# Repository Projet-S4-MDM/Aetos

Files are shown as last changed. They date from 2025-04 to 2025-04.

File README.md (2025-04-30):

# Aetos

Aetos is a vision-abled cable robot designed by 6 robotics engineering students from [Sherbrooke University](https://www.usherbrooke.ca/).

## Original Contributors

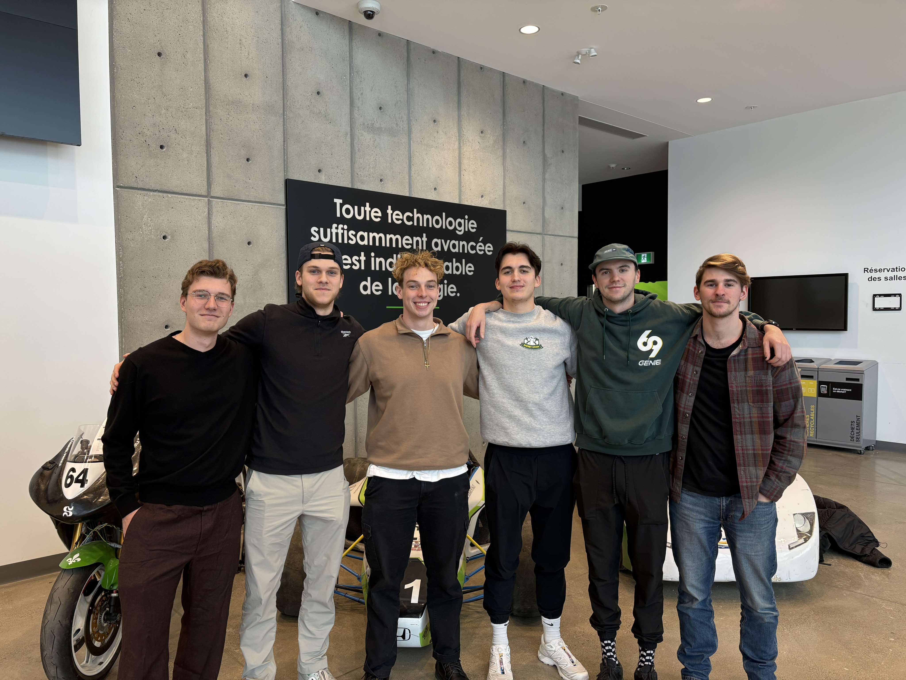
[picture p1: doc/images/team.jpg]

**From left to right:** Mathys Bousquet, Nathan Dumoulin, Édouard Lebel-Bernier, Nikolay Papanchez, Émile Savoie and David Ferron

## Final Product
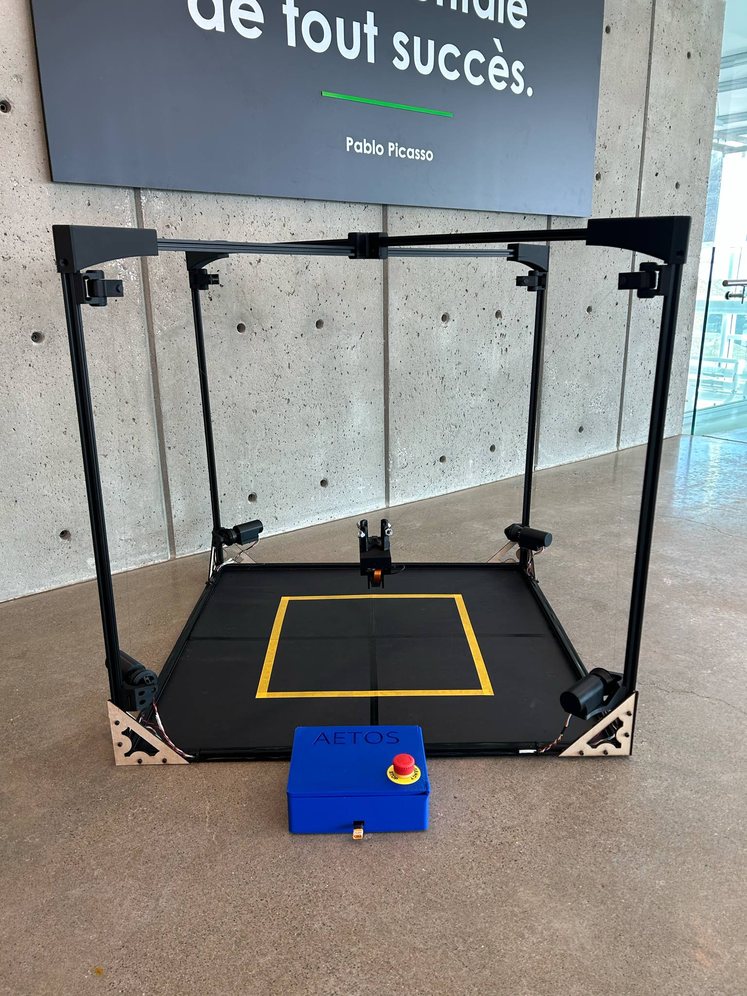
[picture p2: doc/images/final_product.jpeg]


## Documentation

The following links contain the documentation to build and operate the different elements of Aetos from scratch:

- [Mechanical Assembly](doc/Mechanical/mecanical_assembly.md)
- [Electrical Assembly](doc/Electrical/electrical_assembly.md)
- [Software Setup](doc/Software/setup.md)
- [Micro controller Setup](doc/Software/esp32-platformio-setup.md)
- [Usage](doc/Software/usage.md)

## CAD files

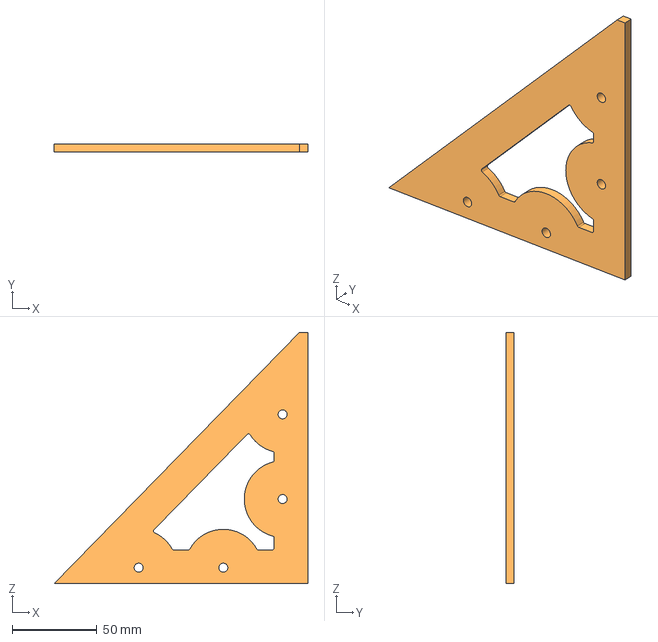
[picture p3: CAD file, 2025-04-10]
doc/Mechanical/STEP/Frame/Frame - Triangle2.step
150.0 x 5.00 x 148.5 mm

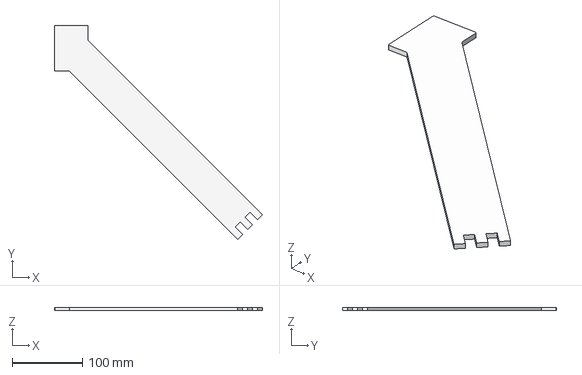
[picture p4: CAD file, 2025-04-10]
doc/Mechanical/STEP/Homing/Frame - Homing3.step
296.6 x 305.1 x 4.76 mm

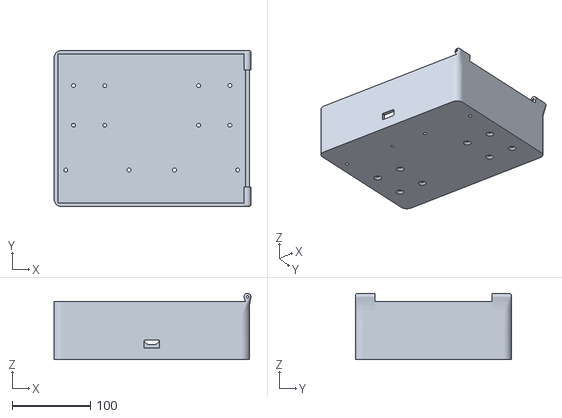
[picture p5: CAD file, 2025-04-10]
doc/Mechanical/STL/Electrical_box/Box - Box.stl
252.0 x 200.0 x 85.0

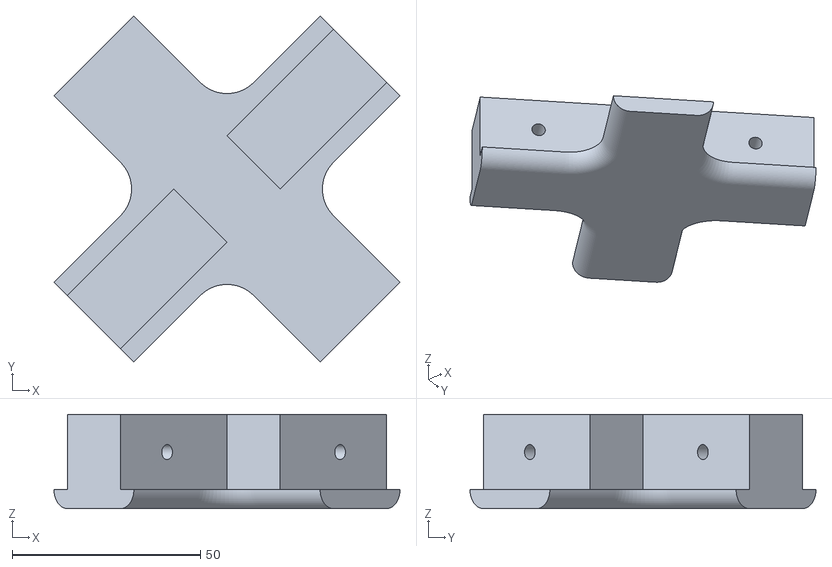
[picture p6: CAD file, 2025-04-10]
doc/Mechanical/STL/Frame/Frame - Top_middle2.stl
91.9 x 91.9 x 25.0

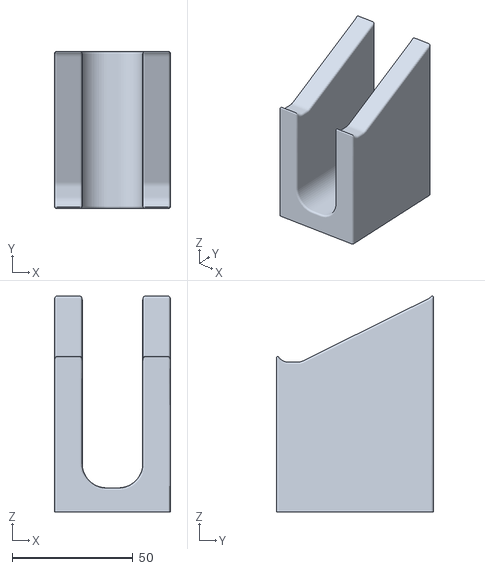
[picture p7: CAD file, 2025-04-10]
doc/Mechanical/STL/Homing/Frame - Homing1.stl
48.0 x 65.0 x 89.3

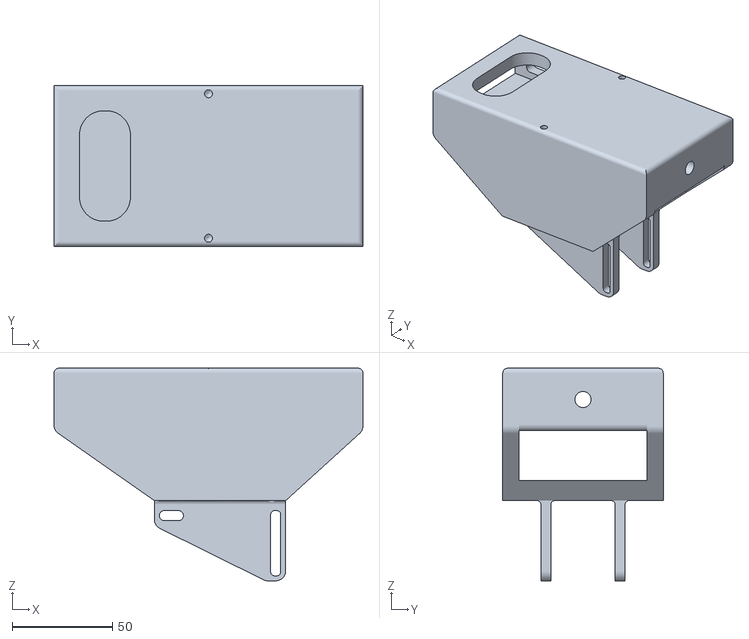
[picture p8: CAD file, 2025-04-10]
doc/Mechanical/STL/Payload/Payload - Body.stl
154.0 x 80.0 x 106.0

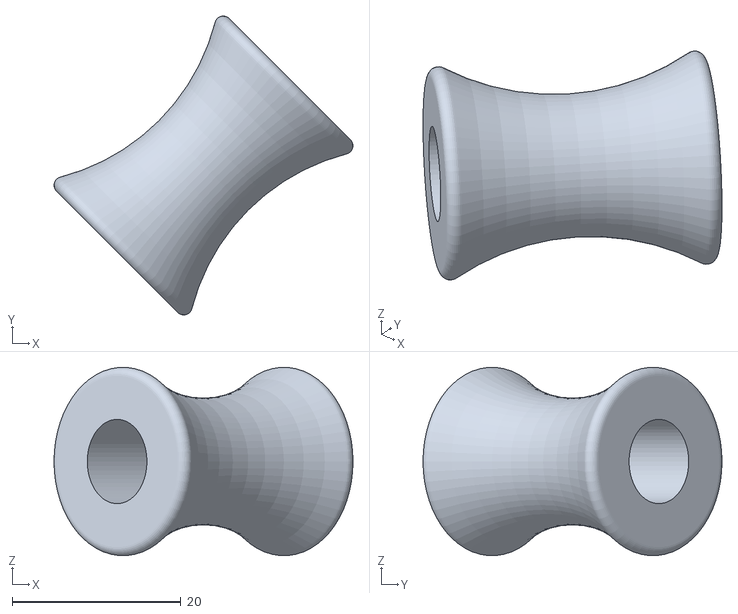
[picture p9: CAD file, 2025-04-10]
doc/Mechanical/STL/Pulley/Pulley - Pulley.stl
35.5 x 35.5 x 22.3

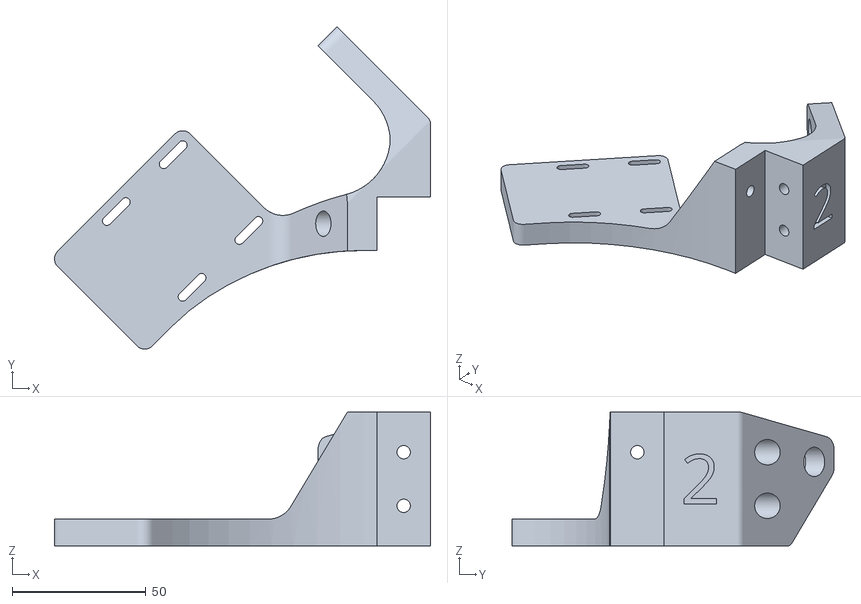
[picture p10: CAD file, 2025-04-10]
doc/Mechanical/STL/Winch/Winch - Motor support(2).stl
140.4 x 120.3 x 50.0

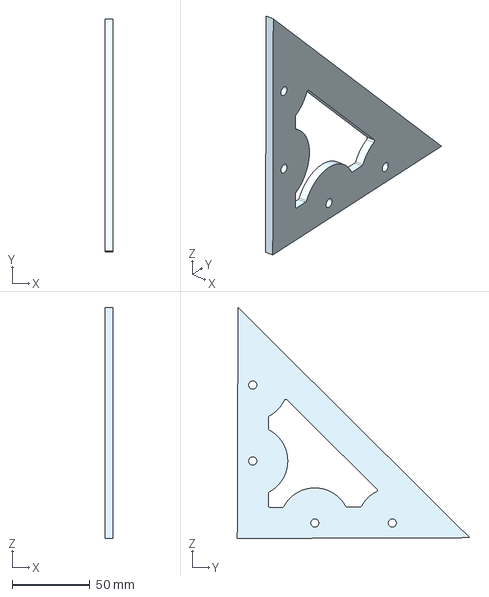
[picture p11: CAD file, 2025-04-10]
doc/Mechanical/STEP/Frame/Frame - Triangle1.step
5.00 x 150.0 x 149.0 mm

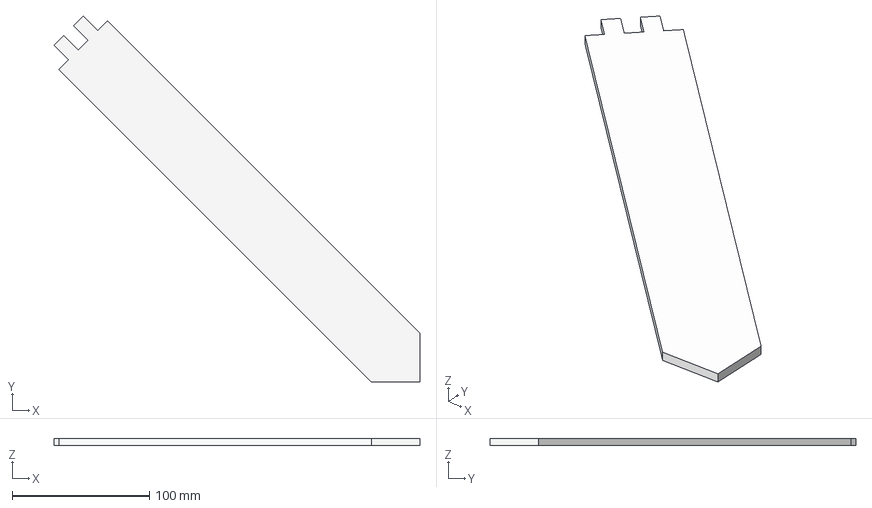
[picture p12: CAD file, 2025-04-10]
doc/Mechanical/STEP/Homing/Frame - Homing2.step
266.3 x 266.3 x 4.76 mm

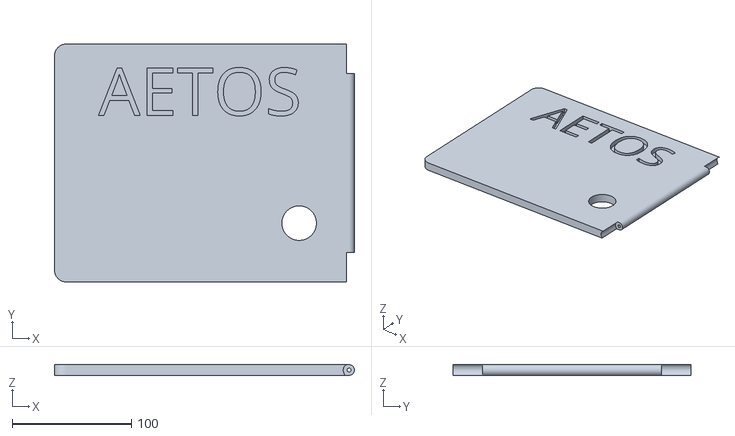
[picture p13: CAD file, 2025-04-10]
doc/Mechanical/STL/Electrical_box/Box- Door.stl
252.0 x 200.0 x 9.00

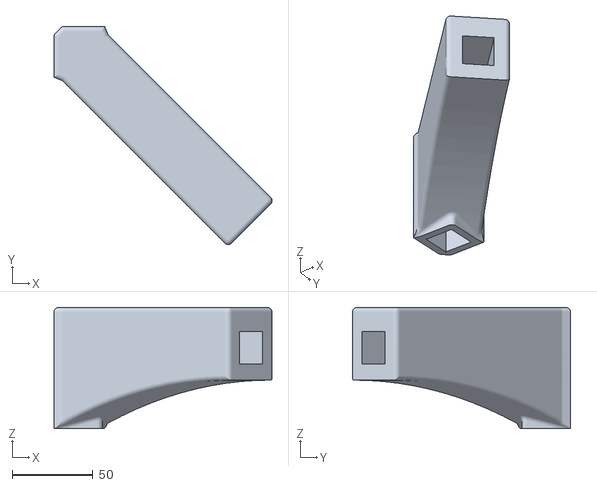
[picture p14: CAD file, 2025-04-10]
doc/Mechanical/STL/Frame/Frame - Top_Frame2.stl
134.8 x 134.8 x 75.0

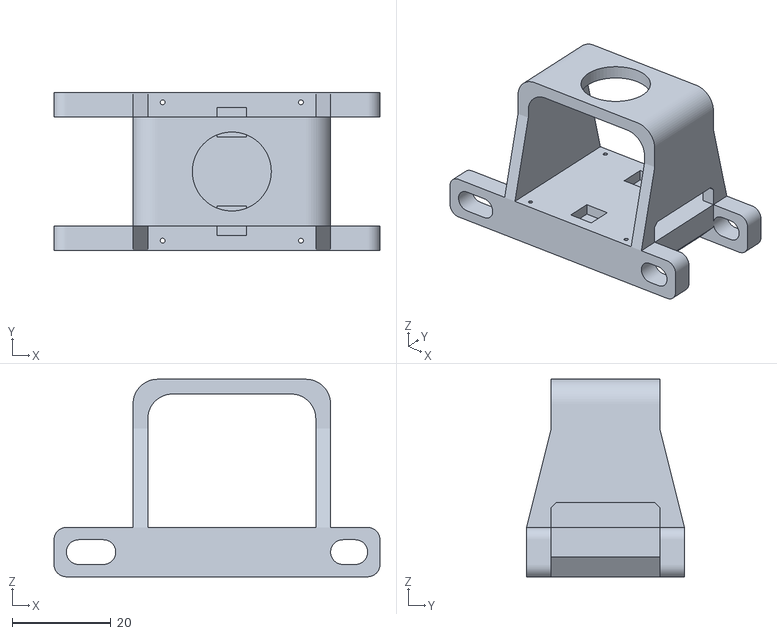
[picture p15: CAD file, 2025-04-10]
doc/Mechanical/STL/Payload/Payload - pi_camera.stl
66.0 x 32.0 x 40.0

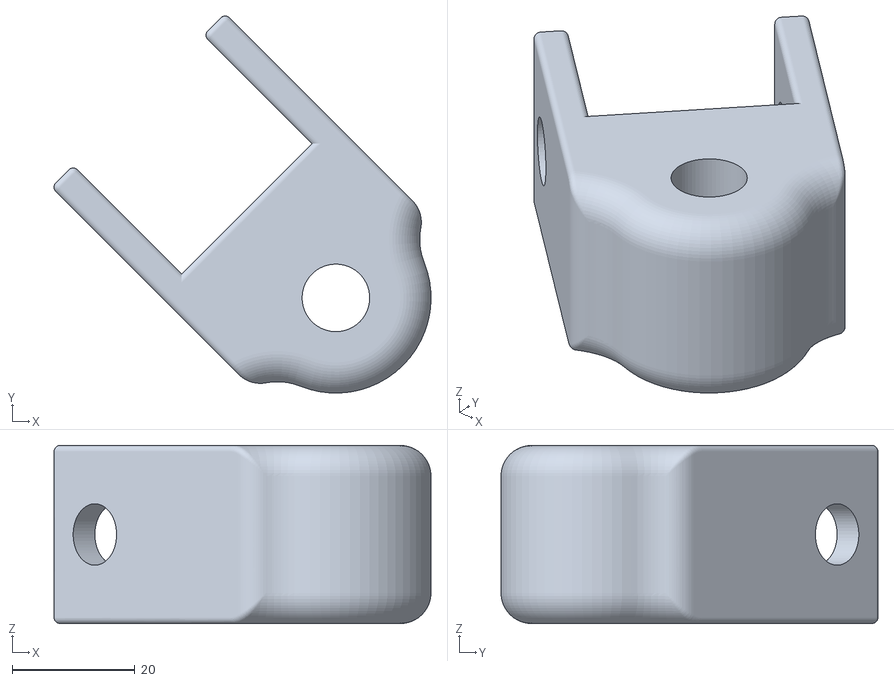
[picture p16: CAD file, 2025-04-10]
doc/Mechanical/STL/Pulley/Pulley - Pulley support.stl
61.4 x 61.4 x 29.0

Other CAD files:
doc/Mechanical/STL/Winch/Winch - motor support(4).stl
doc/Mechanical/STL/Frame/Frame - Top_middle1.stl
doc/Mechanical/STL/Payload/Payload - Attachment.stl
doc/Mechanical/STL/Pulley/Pulley - Top hinge.stl
doc/Mechanical/STL/Frame/Frame - Top_Frame1.stl
doc/Mechanical/STL/Pulley/Pulley - Hinge.stl
doc/Mechanical/STL/Pulley/Pulley - Pin pulley.stl
doc/Mechanical/STL/Pulley/Pulley - under hinge.stl
doc/Mechanical/STL/Winch/Winch - Casing cover.stl
doc/Mechanical/STL/Winch/Winch - Motor Casing.stl
doc/Mechanical/STL/Winch/Winch - Motor Support (1).stl
doc/Mechanical/STL/Winch/Winch - Motor support(3).stl
doc/Mechanical/STL/Winch/Winch - Winch.stl

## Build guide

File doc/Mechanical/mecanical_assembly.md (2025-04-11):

# Mechanical Assembly Guide

This project consists of five main subsystems that must be assembled to complete the system:

- 4 pulleys  
- 4 winches  
- 1 frame  
- 1 payload  
- 1 homing tool

Once assembled, your build should look like the image below:

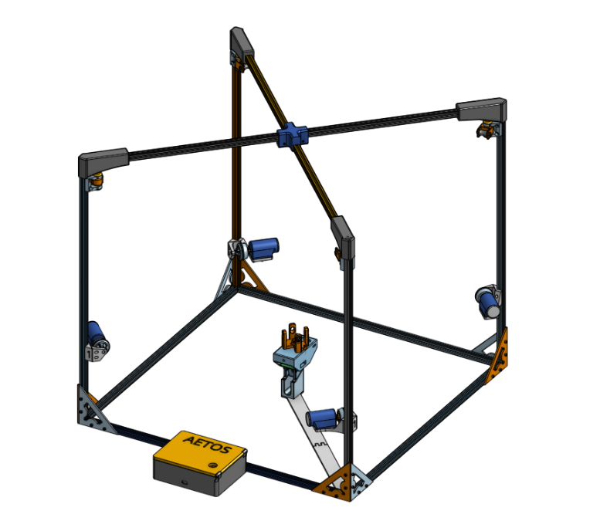
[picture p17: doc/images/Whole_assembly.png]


## Table of Contents

1. [Bill of Materials (BOM)](#1-bill-of-materials-bom)  
2. [Frame Assembly](#2-frame-assembly)  
3. [Winch Subsystem](#3-winch-subsystem)  
4. [Pulley Subsystem](#4-pulley-subsystem)  
5. [Completing the Frame](#5-completing-the-frame)  
6. [Electrical Box](#6-electrical-box)  
7. [Homing Tool](#7-homing-tool)  
8. [Payload](#8-payload)  
9. [Final Assembly](#9-final-assembly)  

---

## 1. Bill of Materials (BOM)

This project uses a combination of 3D printed parts, laser-cut plywood, and off-the-shelf components.

- A 3D printer with a minimum bed size of **20cm x 20cm** is required, capable of printing in **PLA and TPU**.
- A **laser cutter** is needed for some parts.

| Description | Quantity | Link |
| --- | --- | --- |
| 20mm x 1000mm aluminium extrusion | 6 | |
| 20mm x 1220mm aluminium extrusion | 2 | |
| 90° 3-way aluminium extrusion connector | 4 | [Amazon](https://www.amazon.ca/dp/B08C9Q2TGW) |
| M5 x 5mm set screw | 16 | |
| M5 T-nuts for 20mm extrusion | 62 | |
| M5 x 10mm socket head screw | 62 | |
| M3 x 6mm x 5mm brass insert | 20 | |
| M3 x 10mm countersunk screw | 4 | |
| M3 x 10mm socket head screw | 20 | |
| M3 x 20mm socket head screw | 6 | |
| M3 x 30mm socket head screw | 2 | |
| M4 x 16mm socket head screw | 4 | |
| M3 nut | 8 | |
| M2 x 10mm socket head screw | 4 | |
| M2 washer | 4 | |
| 6-32 x 1" machine screw | 16 | |
| Aluminium hub for 6mm D-shaft | 4 | [link](https://ca.robotshop.com/products/servocity-1310-series-hyper-hub-6mm-d-bore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) |
| 8lb braided fishing line | 1 roll | |
| Super glue | small amount | |
### File Resources

- STL files for 3D printing: [`/doc/STL`](../doc/STL)  
- STEP files for laser cutting or modification if you don't own a laser cutter : [`/doc/STEP`](../doc/STEP)

Access the full CAD model via Onshape:  
[Onshape Link](https://cad.onshape.com/documents/390c295f6aa4808e63a0329a/w/15b9467409059843a81b2a98/e/3b631072c0b4a11c9089c144)

---

## 2. Frame Assembly

You will need to 3D print the parts in [`/doc/STL/Frame`](../doc/STL/Frame) and laser cut the parts in [`/doc/STEP/Frame`](../doc/STEP/Frame).

### Required Parts

#### 3D Printed

| Name | Quantity |
|---|---|
| Top_Frame1 | 2 |
| Top_Frame2 | 2 |
| Top_Middle1  | 1 |
| Top_Middle2  | 1 |
| Triangle1 | 4 |
| Triangle2 | 4 |

#### Hardware

| Name | Quantity |
|---|---|
| M3 x 6mm x 5mm brass insert  | 16 |
| M5 x 5mm set screw | 12 |
| M3 x 10mm socket head screw  | 4 |

### Step-by-Step

#### Step 1
Assemble the 6 aluminium extrusions (1000mm) using the 4 corner connectors as shown below:

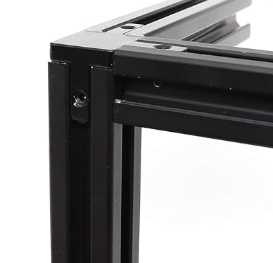
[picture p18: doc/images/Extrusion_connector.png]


You should now have a basic frame like this:

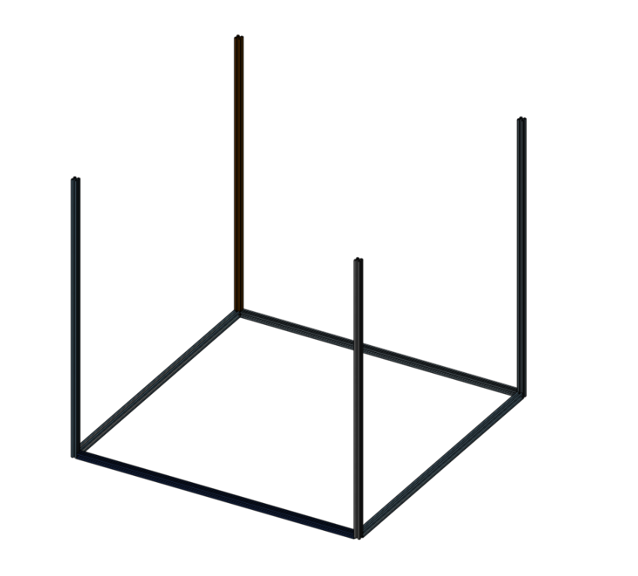
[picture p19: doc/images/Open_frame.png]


Secure the extrusions in place with the M5 set screws.

#### Step 2
Install the triangle brackets using M5 x 10mm screws and loosely attached T-nuts. Align the T-nuts with the extrusion slots, insert, and tighten.

Each corner should look like this:

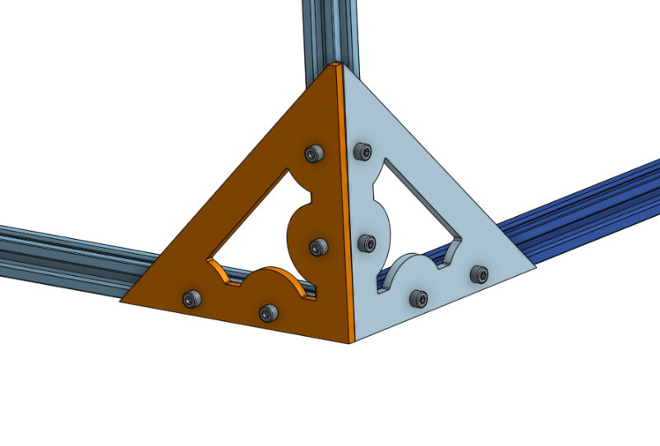
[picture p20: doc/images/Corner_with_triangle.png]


---

## 3. Winch Subsystem

3D print all the files in [`/doc/STL/Winch`](../doc/STL/Winch) 4 times, but print the motor support variants only once each.

### Required Components

| Name | Quantity |
| --- | --- |
| M3 x 6mm x 5mm brass insert | 16 |
| M3 x 10mm screw | 16 |
| M5 x 10mm screw | 12 |
| M5 T-nuts | 12 |
| 6-32 x 1" screw | 16 |
| Aluminium hub for 6mm shaft | 4 |

### Step-by-Step

#### Step 1
Insert the brass inserts into the underside of the motor casing.

#### Step 2
Assemble the winch following this exploded diagram:

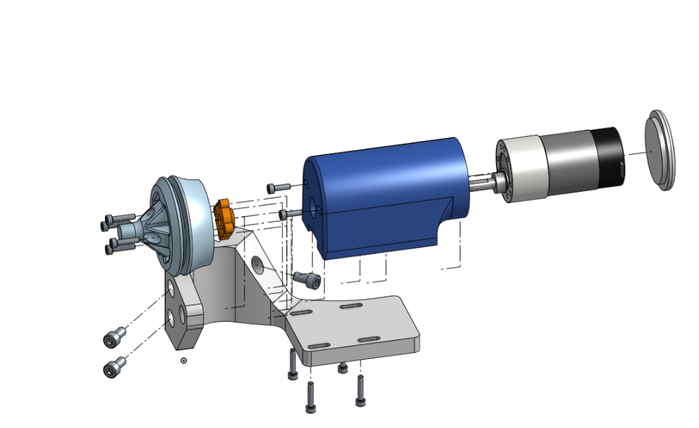
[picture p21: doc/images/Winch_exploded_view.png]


#### Step 3
Attach each winch to the frame using M5 screws and T-nuts. Align with the slots and tighten at the desired height.

Final result:

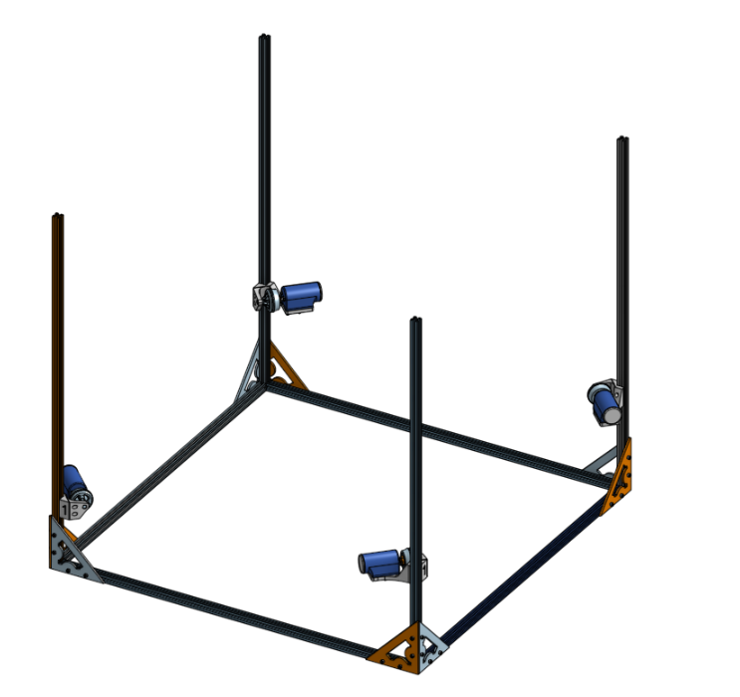
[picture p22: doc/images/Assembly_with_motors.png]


---

## 4. Pulley Subsystem

3D print each file in [`/doc/STL/Pulley`](../doc/STL/Pulley) 4 times.

### Required Components

| Name | Quantity |
|---|---|
| M5 x 10mm screw | 16 |
| M5 T-nuts | 16 |
| M3 x 10mm countersunk screw  | 4 |
| M2 x 10mm socket head screw  | 4 |

### Step-by-Step

#### Step 1
Assemble each pulley using the exploded view:

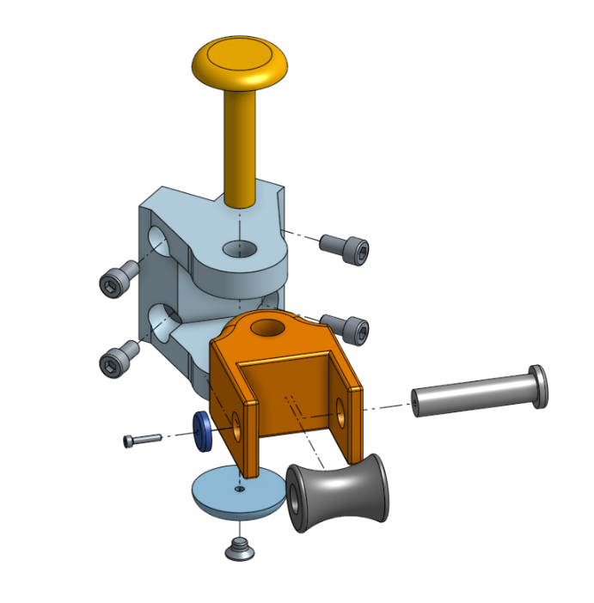
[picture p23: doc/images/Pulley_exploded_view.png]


Note: Screws are driven directly into plastic; apply firm pressure if needed.

#### Step 2
Mount pulleys on the frame using M5 screws and T-nuts.

Final result:

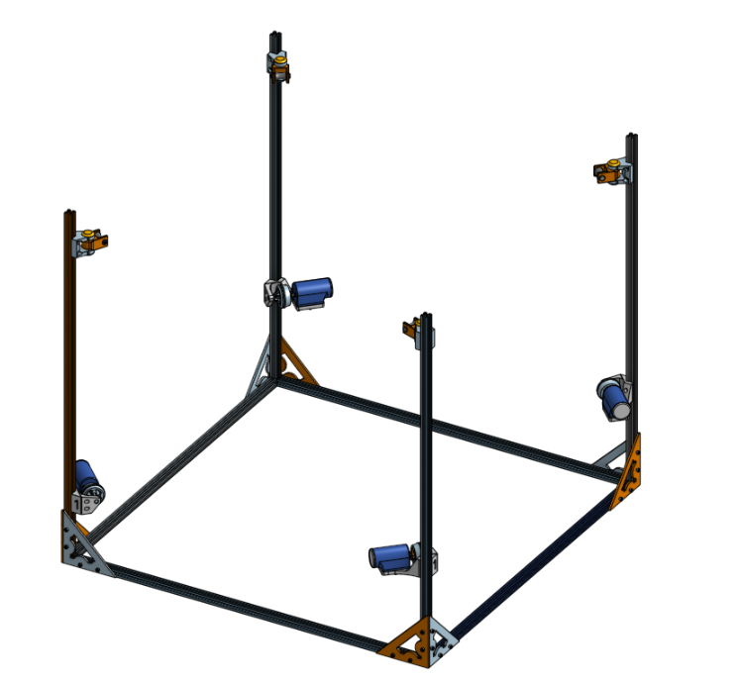
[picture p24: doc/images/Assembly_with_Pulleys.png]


---

## 5. Completing the Frame

### Steps

1. Attach a `Top_Frame1` to each side of a 1220mm extrusion.  
2. Repeat with `Top_Frame2`.  
3. Assemble as shown below:

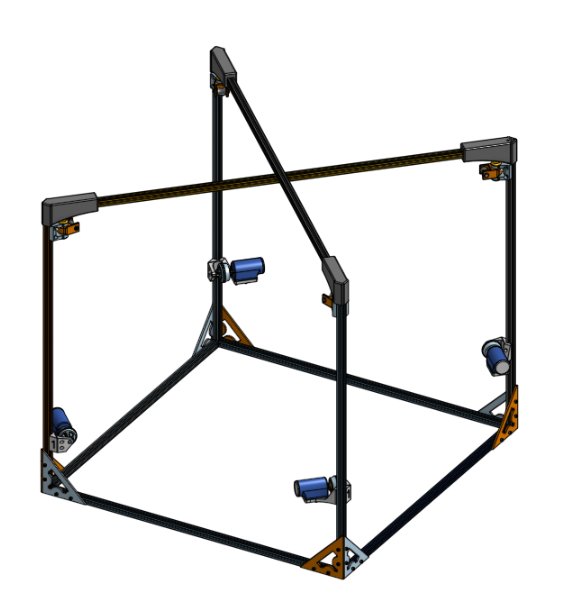
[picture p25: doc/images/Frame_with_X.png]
   

4. Insert brass inserts into `Top_Middle1`.  
5. Attach `Top_Middle2` using M3 x 10mm screws.

Final frame:

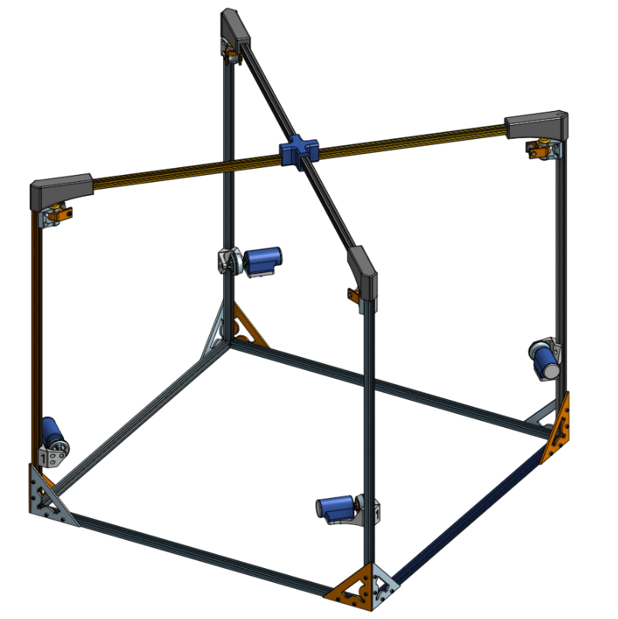
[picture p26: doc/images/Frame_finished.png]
   

---

## 6. Electrical Box

Print each part in [`/doc/STL/Electrical_box`](../doc/STL/Electrical_box). Modify as needed to fit your electronics.

### Required Components

- 2 M3 x 30mm screws

### Steps

1. Secure electronics using screws.  
2. Wire according to the diagram in [`/doc/Electrical`](../doc/Electrical).  
3. Mount the E-stop button on the cover.  
4. Insert two M3 x 30mm screws into each hinge side of the box.

---

## 7. Homing Tool

Print the parts from:

- [`/doc/STL/Homing`](../doc/STL/Homing) 

Laser print the parts from:

- [`/doc/STEP/Homing`](../doc/STEP/Homing)

### Step

Glue the 3D printed part onto the part labeled `homing3`.

Final result:

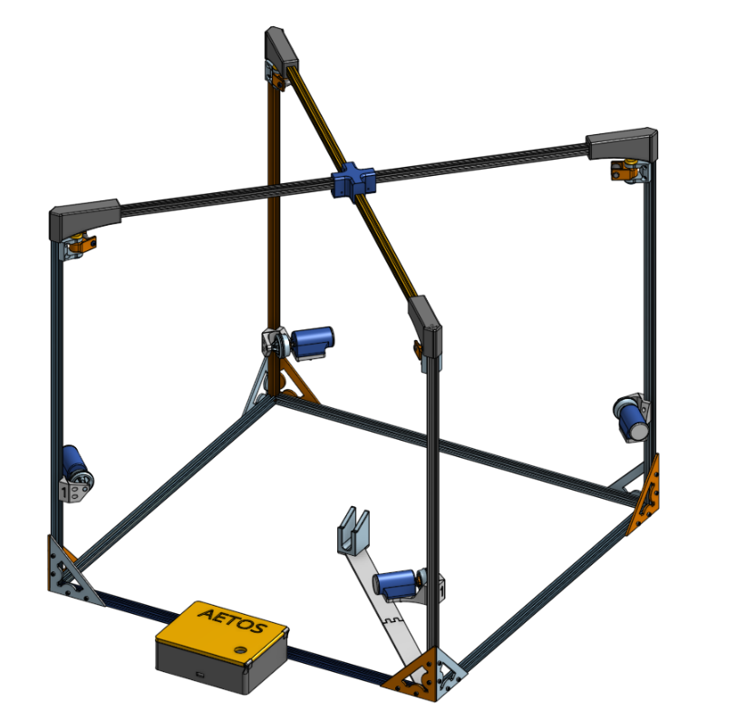
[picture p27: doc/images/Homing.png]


---

## 8. Payload

The payload houses the Raspberry Pi, Pi-camera, and battery.

Files available here: [`/doc/STL/Payload`](../doc/STL/Payload)

### Recommended:  
Print attachment parts in TPU for better flexibility (PLA is acceptable).

### Required Components

| Name | Quantity |
| --- | --- |
| M3 x 6mm x 5mm brass insert | 2 |
| M3 nut | 8 |
| M3 x 20mm socket head screw | 6 |
| M4 x 16mm socket head screw | 4 |

### Steps

1. Insert brass inserts into the top of the payload body.  
2. Slide the Pi camera into its holder and connect the cable.  
3. Assemble the payload using the exploded view:

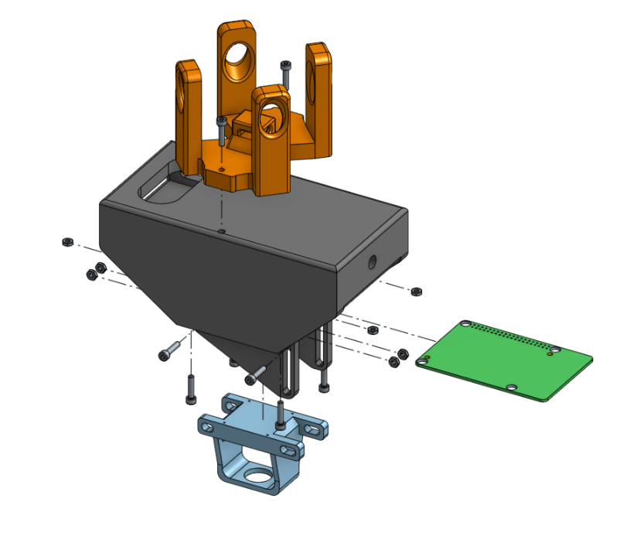
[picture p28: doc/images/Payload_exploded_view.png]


4. Insert the battery into the upper compartment.  
5. Connect the Raspberry Pi to the battery and camera.

---

## 9. Final Assembly

You're now ready to string the fishing line.

### Required Components

| Name | Quantity |
|---|---|
| Fishing line | 1 roll |
| M2 washer | 4 |

### Step-by-Step

#### Step 1
Pass the fishing line through the winch pulley’s small hole. Use tweezers if needed. Tie a knot around a M2 washer to prevent slippage and wind ~2–3m of line onto the pulley. Repeat for all winches.

#### Step 2
Route the line through the pulleys and attachment holes. Tie knots and test their strength.

---

## Congratulations

You’ve completed the full mechanical assembly.

---

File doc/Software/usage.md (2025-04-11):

# Aetos Development Environment

## Table of Contents

- [Opening the Devcontainer](#opening-the-devcontainer)  
- [Development Inside the Container](#development-inside-the-container)  
- [Running the Code](#running-the-code)  
- [Simulation Mode](#simulation-mode)  
- [Controls](#controls)  
- [Homing Procedure](#homing-procedure)  
- [Graphical Interface](#graphical-interface)  
- [Vision System](#vision-system)  

---

## Opening the Devcontainer

When VS Code detects the devcontainer configuration, a notification will appear in the bottom-right corner. Click **"Reopen in Container"** to launch the devcontainer.

Alternatively, you can:

1. Press `Ctrl + Shift + P`  
2. Type `"Dev Containers: Reopen in Container"`  
3. Press Enter  

> **Note:** Opening the container for the first time or rebuilding the environment may take a few minutes. Sit back, relax, and enjoy the nonsense logs in the terminal.

---

## Development Inside the Container

Inside the container, all dependencies specified in the `Dockerfile` are available.

- **Terminator** is installed (a terminal multiplexer useful for ROS2 development). To launch it, open a VSCode terminal and run:
  
  ```bash
  terminator
  ```

- The `.bashrc` file includes a helper command to build the ROS2 workspace easily. Simply run:
  
  ```bash
  b
  ```

---

## Running the Code

To launch the full application (including nodes and GUI), run:

```bash
ros2 launch aetos_auxiliary aetos.launch.py
```

> **Note:** This will only send motor commands if the computer is connected to the ESP32 via serial port.

---

## Simulation Mode

For development purposes, Aetos also supports a simulation mode. To launch it, use: modify the aetos.launch.py launch file to integrate it in the launch.

---

## Controls

Aetos is controlled using a Bluetooth controller. Keybindings can be modified in the `joy_demux.py` file located in the `aetos_joy` ROS2 package.

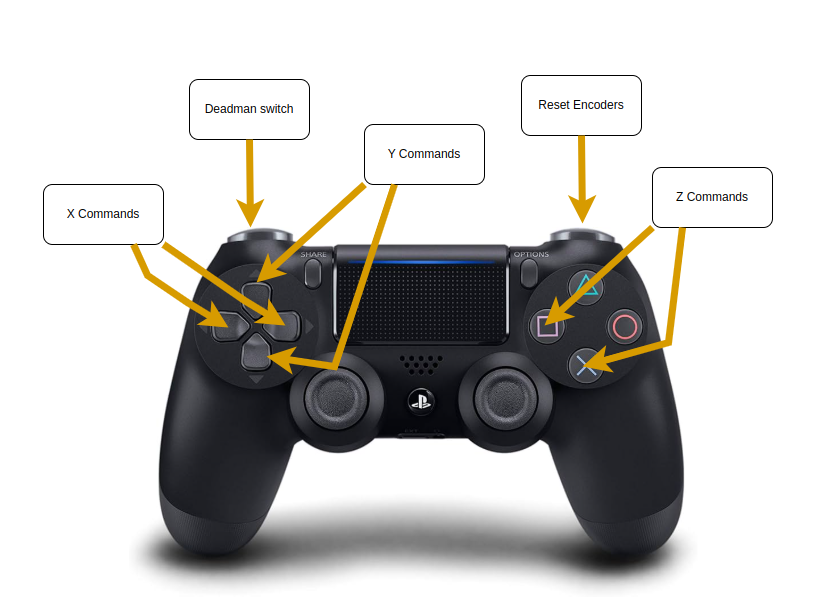
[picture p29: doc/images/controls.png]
Controller


---

## Homing Procedure

To prevent error accumulation and drift, Aetos requires homing every time it is restarted.

1. Place the payload on the designated homing area (see [Mechanical Assembly](../Mechanical/mecanical_assembly.md)).
2. Use the controller to reset the encoders.

> **Caution:** Ensure motor power is **disconnected** before resetting encoders to avoid unintended movement or damage.

---

## Graphical Interface

The GUI allows users to:

- Toggle between control modes
- Activate a software emergency stop (E-Stop)
- Monitor linear velocity and payload position

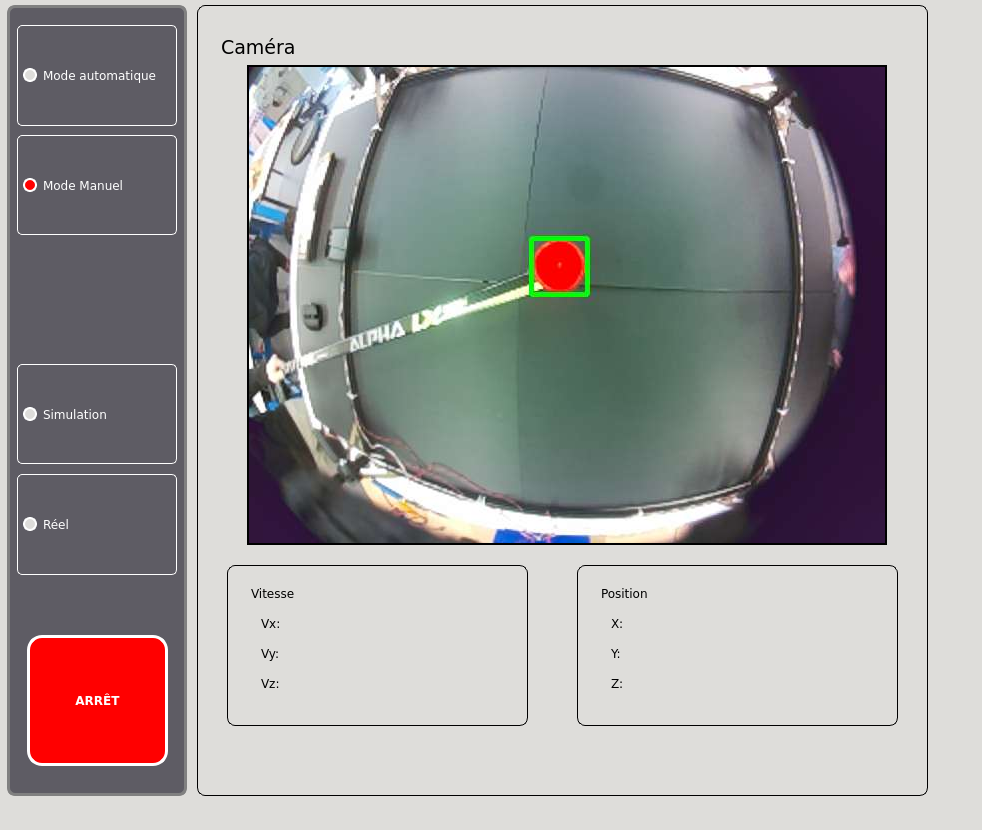
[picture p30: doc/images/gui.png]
GUI


---

## Vision System

To enable vision:

1. Ensure all relevant nodes are launched.
2. Establish a successful connection between the main computer and the Raspberry Pi.
3. Once connected, the camera feed will appear in the GUI.
4. Use the GUI buttons to toggle between teleoperation and autonomous control.

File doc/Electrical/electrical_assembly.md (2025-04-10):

# Electrical Assembly

## Build of Material

| Item | Description | Quantity | Unit Price | Total Price | Link |
|---|---|---|---|---|---|
| 1 | Freenove ESP32-S3-WROOM Board Lite | 1  | $15.00  | $15.00  | [Link](https://www.amazon.ca/Freenove-ESP32-S3-WROOM-Dual-core-Microcontroller-Wireless/dp/B0DHJZ1V81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) |
| 2 | Freenove Breakout Board for ESP32 | 1  | $18.00  | $18.00  | [Link](https://www.amazon.ca/Freenove-Breakout-ESP32-S3-Terminal-Outputs/dp/B0CD2512JV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) |
| 3 | FIT0186 DC Motor | 4  | $26.59  | $106.36 | [Link](https://www.digikey.ca/en/products/detail/dfrobot/FIT0186/6588528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) |
| 4 | Talon SRX Motor Controller | 4  | $131.00 | $524.00 | [Link](https://store.ctr-electronics.com/products/talon-srx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) |
| 5 | 35A Terminal Block (6 Position, Screw) | 2  | $7.00 | $14.00 | [Link](https://www.amazon.ca/Joinfworld-Terminal-Position-Pre-Insulated-Jumper/dp/B0B24FZWPH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) |
| 6 | Emergency Stop Push Button (10A) | 1  | $17.00 | $17.00 | [Link](https://www.amazon.ca/mxuteuk-HB2-ES544-Mushroom-Emergency-Warranty/dp/B07R8PTTDX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) |
| 7 | Raspberry Pi 5 | 1  | $179.99$ | $179.99$ | [Link](https://www.amazon.ca/-/fr/dp/B0CTF9GKMR?ref_=ppx_hzsearch_conn_dt_b_fed_asin_title_4) |
| 8 | PiCam V3 | 1  | $35.00$ | $35.00$ | [Link](https://www.pishop.ca/product/raspberry-pi-camera-module-3/?searchid=0) |
| 9 | Battery  | 1  | $34.00$ | $34.00$ | [Link](https://www.amazon.ca/Charmast-Batterie-compatible-smartphones-tablettes/dp/B09WHPDB6C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) |

**Total:** 942.99$$

**Note:** We are using Talon SRX motor controllers because we had them for free. They are largely overkill for our application, as they offer advanced features like current sensing and CAN bus communication, which are not necessary for our setup. If you are building a similar system from scratch, a simpler and more cost-effective motor driver would be a better choice.

## Wiring Overview

- **Motor Power Supply:**  
  We will be using a DC power source rated for a maximum of 6.4A, connected via an XT60 connector. XT60 was chosen as it was readily available, but any connector rated for at least 6.4A will suffice.

- **ESP32 Power Supply:**  
  The ESP32 board is powered through its USB-C port, which also facilitates serial communication.

- **Grounding:**  
  All the grounds (GND) of the devices must be connected together at a single point via a terminal block. This ensures a common reference for all components.

- **12V Power Distribution:**  
  Devices that operate on 12V (such as the DC motors and the Talon SRX motor controllers) should be connected to a dedicated 12V terminal block. This keeps the high-power components separate from the low-power ones (like the ESP32) and helps ensure proper voltage distribution to each device.

- **Emergency Stop Button Placement:**  
  The Emergency Stop (e-stop) button should be placed between the 12V power source and the 12V terminal block. This ensures that if the e-stop is pressed, it will immediately cut off the power to the 12V components, providing an effective safety measure.

- **Payload Setup**
  The payload consists of a Raspberry Pi 5, a Pi Camera V3, and a power pack. The Raspberry Pi 5 operates at 5V and requires a minimum of 3A, which the power pack is capable of supplying. But you need to use a short cable with low resistance. 
  - Connect the Raspberry Pi to the power pack using a USB to USB-C cable.
  - Connect the Pi Camera V3 to the Raspberry Pi 5.

---

### Wiring Steps:
1. **Connect the ESP32 to the Breakout Board:**  
   Begin by securely plugging the ESP32 board into the breakout board.

2. **PWM Motor Control:**  
   Next, connect the PWM pins of the Talon motor controllers to the appropriate GPIO pins on the ESP32.

3. **Encoder Connections:**  
   Afterward, wire the encoder pins to the corresponding GPIO pins on the ESP32.

4. **Connect Grounds:**  
   All the ground (GND) pins from the ESP32, motor controllers, and other components must be connected to a single terminal block to establish a common ground.

5. **Connect 12V Devices:**  
   The devices that need 12V power (DC motors, Talon SRX controllers, etc.) should be connected to the 12V terminal block, ensuring they receive the correct voltage.

6. **Place the Emergency Stop Button:**  
   Position the E-stop button between the 12V power source and the 12V terminal block. This will allow it to cut power to the 12V components if activated.

---

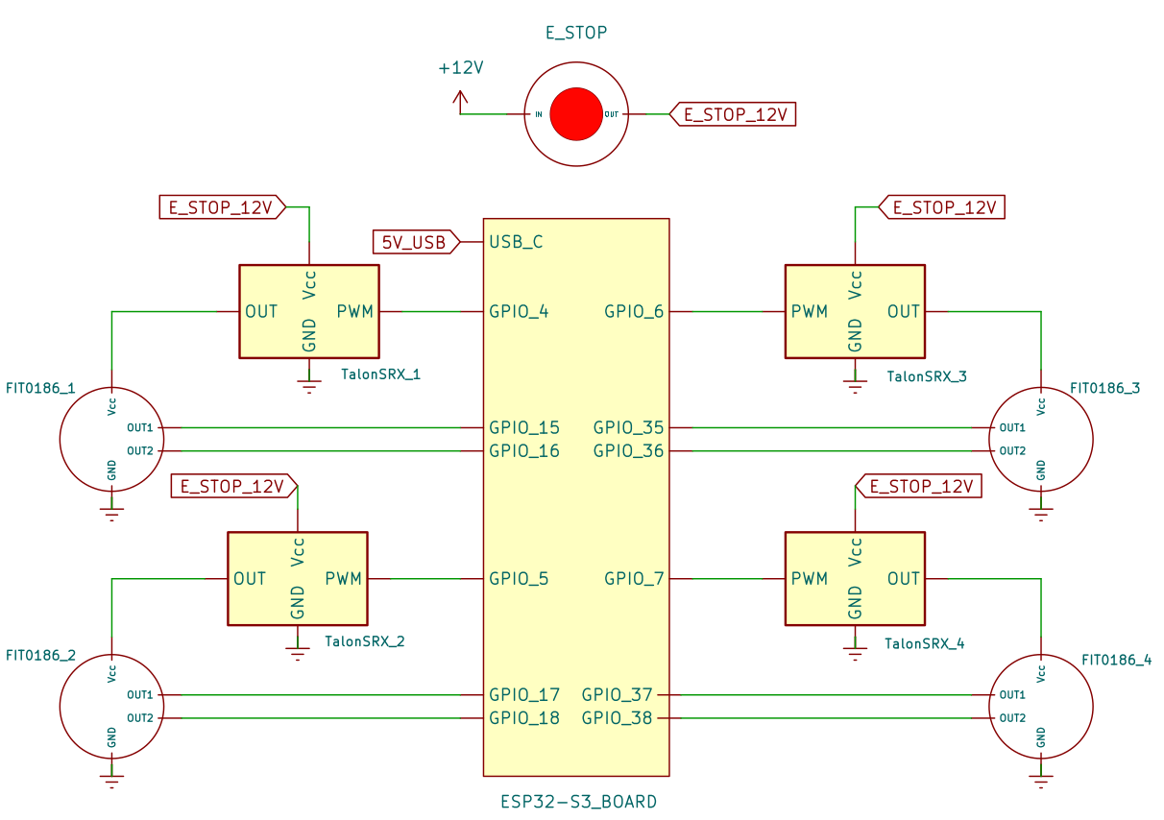
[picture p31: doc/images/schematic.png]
Motor Driver


--- 

### Additional Recommendations
- Ensure all connections are properly insulated, particularly the power supply and motor controller pins, to prevent short circuits.

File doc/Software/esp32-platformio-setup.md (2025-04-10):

# ESP32-S3 Setup with PlatformIO
This guide explains how to set up PlatformIO to develop for the ESP32-S3-DevKitC-1 using the Arduino framework.

---
## Prerequisites

- [Visual Studio Code](https://code.visualstudio.com/)
- Internet connection
---
## 1. Install PlatformIO

1. Open **Visual Studio Code**
2. Go to the **Extensions** tab (or press `Ctrl+Shift+X`)
3. Search for **"PlatformIO IDE"** and install it
4. Restart VS Code if prompted
---
## 2. Open the Project

Open the project by opening the `aetos-micro` folder with PlatformIO:

1. Launch **Visual Studio Code**
2. Click on **File > Open Folder...**
3. Select the `aetos-micro` folder that contains the code and the `platformio.ini` file
4. PlatformIO will automatically recognize and load the project
---
## 3. How to Upload to the ESP32

To flash the code to your ESP32-S3 board:
### Step-by-step:

1. Connect your ESP32-S3 board to your computer via USB
2. Make sure the board is detected by your system
3. In Visual Studio Code, locate the PlatformIO toolbar at the bottom
4. Click the right arrow icon (labeled `Upload`) to compile and flash the code to the board
5. Wait for the upload to complete
---
### platformio.ini Configuration

Ensure your `platformio.ini` file looks like this:

```ini
[env:esp32-s3-devkitc-1]
platform = https://github.com/Jason2866/platform-espressif32.git#Arduino/IDF5
board = esp32-s3-devkitc-1
framework = arduino

monitor_speed = 115200
monitor_raw = true

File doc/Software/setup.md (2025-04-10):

# Software setup

## Table of Contents
- [Prerequisites](#prerequisites)
- [Docker Installation](#docker-installation)
- [VS Code Setup](#vs-code-setup)
- [Raspberry Pi 5 Setup](#raspberry-pi-5-setup)  
  - [Setup of the Raspberry Pi](#setup-of-the-raspberry-pi)  
  - [Setup the Pi Camera](#setup-the-pi-camera)  
  - [IP Setup](#ip-setup)
- [You're now ready to use the software](#youre-now-ready-to-use-the-software)

## Prerequisites

The Aetos software runs on [Ubuntu 22.04](https://releases.ubuntu.com/jammy/). To facilitate dependency management, the project runs with [docker](https://www.docker.com/). The repository contains a custom image containing all necessary requirements for the project.

## Docker Installation

1. Set up Docker's apt repository:

```bash
# Add Docker's official GPG key:
sudo apt-get update
sudo apt-get install ca-certificates curl
sudo install -m 0755 -d /etc/apt/keyrings
sudo curl -fsSL https://download.docker.com/linux/ubuntu/gpg -o /etc/apt/keyrings/docker.asc
sudo chmod a+r /etc/apt/keyrings/docker.asc

# Add the repository to Apt sources:
echo \  
  "deb [arch=$(dpkg --print-architecture) signed-by=/etc/apt/keyrings/docker.asc] https://download.docker.com/linux/ubuntu \  
  $(. /etc/os-release && echo "$VERSION_CODENAME") stable" | \  
sudo tee /etc/apt/sources.list.d/docker.list > /dev/null
sudo apt-get update
```

To install the latest version, run:

```bash
sudo apt-get install docker-ce docker-ce-cli containerd.io docker-buildx-plugin docker-compose-plugin
```

Create the Docker group:

```bash
sudo groupadd docker
```

Add your user to the Docker group:

```bash
sudo usermod -aG docker $USER
```

**Reboot your computer to enable changes to groups.**

## VS Code Setup

Install the necessary VS Code extensions by running the following command in your terminal:

```bash
code --install-extension ms-vscode-remote.remote-containers
code --install-extension ms-azuretools.vscode-docker
code --install-extension ms-vscode-remote.remote-ssh
```

## Raspberry Pi 5 Setup
The Raspberry Pi is powered by a 5V 3A power pack and runs on the Raspberry Pi 64-bit OS. A [Raspberry Pi Camera V3](https://www.pishop.ca/product/raspberry-pi-camera-module-3/?src=raspberrypi) is being used to enable the vision recognition.

> **Note:** The Pi is currently independant from the docker DevContainer due to compatibility issues regarding the pi camera. The pi camera unfortunately does not run on Ubuntu 24.04 which is the only Ubuntu based operating system that can be flashed for the Pi5.

### 1. Install Raspberry Pi OS (64-bit)

Download the OS from the official Raspberry Pi website:  
[Download Raspberry Pi OS](https://www.raspberrypi.com/software/)

### 2. Setup the Pi Camera

1. Open the terminal:
   ```bash
   sudo raspi-config
   ```
2. Navigate to:  
   `Interface Options` → `Camera` → `Enable`

3. Reboot the Pi to apply changes:
   ```bash
   sudo reboot
   ```

4. Install required Python packages:
   ```bash
   sudo apt update
   sudo apt install python3-pip
   pip install opencv-python websockets numpy picamera2
   ```

### 3. Network Setup

The Raspberry Pi communicates with the main computer via WebSocket. Make sure both devices are on the **same Wi-Fi network**.

1. **Transfer the communication script** to your Raspberry Pi. Find the script [HERE](../Software/Files/aetos_pi.py)

2. **Edit the script to set your PC's IP address:**
   ```bash
   nano aetos_pi.py
   ```
   Locate the line:
   ```python
   SERVER_IP = "127.0.0.1"
   ```
   Replace `127.0.0.1` with your PC’s local IP address (e.g., `192.168.x.x`)

### 5. Auto-Start Script on Boot

1. Open `rc.local`:
   ```bash
   sudo nano /etc/rc.local
   ```

2. Add the following line **before** `exit 0`:
   ```bash
   python3 /home/pi/<your-project-folder>/your_script_name.py &
   ```
   - Replace `<your-project-folder>` and `your_script_name.py` with the actual path and file name.
   - The `&` ensures the script runs in the background.

3. Save and exit:  
   Press `CTRL + X`, then `Y`, then `Enter`.

4. Make sure `rc.local` is executable:
   ```bash
   sudo chmod +x /etc/rc.local
   ```

5. Reboot to verify:
   ```bash
   sudo reboot
   ```

**Done!** Your Raspberry Pi should now start the camera communication script automatically on boot and be ready to send data to your PC.

## You're now ready to use the software
Follow the instructions in the [Usage README](usage.md) to get started.

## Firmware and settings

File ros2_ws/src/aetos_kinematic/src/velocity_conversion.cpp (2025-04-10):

#include <functional>
#include <memory>
#include <Eigen/Dense>
#include "rclcpp/rclcpp.hpp"
#include "aetos_msgs/msg/velocity.hpp"
#include "aetos_msgs/msg/encoder_values.hpp"
#include "aetos_msgs/msg/motor_velocity.hpp"
#include "aetos_msgs/msg/effector_position.hpp"

using std::placeholders::_1;

struct sVelocity
{
  float vx;
  float vy;
  float vz;
};

struct sPosition
{
  float x;
  float y;
  float z;
};

struct sMotorVelocity
{
  float w1;
  float w2;
  float w3;
  float w4;
};

struct sCableLength
{
  float l1;
  float l2;
  float l3;
  float l4;
};

constexpr float LIMIT_BUFFER = 0.1f;
constexpr float LIMIT_Z = 0.1f;

namespace Limits
{
  constexpr float X_MAX = 1.0f - LIMIT_BUFFER;
  constexpr float X_MIN = 0.0f + LIMIT_BUFFER;
  constexpr float Y_MAX = 1.0f - LIMIT_BUFFER;
  constexpr float Y_MIN = 0.0f + LIMIT_BUFFER;
  constexpr float Z_MAX = LIMIT_Z;
  constexpr float Z_MIN = 0.90f;
}

// SETUP
constexpr float PI = 3.14159265359;

constexpr float MAX_WHEEL_VELOCITY = 5.0f;

constexpr float MAX_ACCEL = 3.0f;

constexpr float _radius = 0.05;

constexpr float _arenaLength = 0.95f;
constexpr float _arenaWidth = 0.95f;
constexpr float _arenaHeight = 0.935f;

constexpr sCableLength _initialCableLength = {1.037f, 1.037f, 1.037f, 1.037f};

constexpr sPosition _pole1 = {0.0f, 0.0f, 0.0f};
constexpr sPosition _pole2 = {0.0f, 0.95f, 0.0f};
constexpr sPosition _pole3 = {0.95f, 0.95f, 0.0f};
constexpr sPosition _pole4 = {0.95f, 0.0f, 0.0f};

sVelocity _currentVelocity = {0.0f, 0.0f, 0.0f};

rclcpp::Time _lastVelocityUpdateTime{0, 0, RCL_ROS_TIME};

class VelocityConversion : public rclcpp::Node
{
public:
  VelocityConversion()
      : Node("VelocityConversion")
  {
    _subJoyVelocity = this->create_subscription<aetos_msgs::msg::Velocity>(
        "aetos/control/velocity", 10, std::bind(&VelocityConversion::joyVelocityCallback, this, _1));

    _subEncoder = this->create_subscription<aetos_msgs::msg::EncoderValues>(
        "aetos/control/encoder", 10, std::bind(&VelocityConversion::encoder_callback, this, _1));

    _joyVelPub = this->create_publisher<aetos_msgs::msg::MotorVelocity>("aetos/cmd/velocity", 10);

    _angularVelPub = this->create_publisher<aetos_msgs::msg::MotorVelocity>("aetos/control/angular_velocity", 10);

    _positionPub = this->create_publisher<aetos_msgs::msg::EffectorPosition>("aetos/control/position", 10);
  }

private:
  sVelocity _velocity;
  sPosition _cameraPosition;
  sPosition _positionError = {0.0f, 0.0f, 0.0f};
  sMotorVelocity _motorVelocity;
  sCableLength _cableLength;
  sPosition _desiredPosition = {0.475f, 0.475f, 0.79f};

  void updateVelocity(const aetos_msgs::msg::Velocity &msg);
  void updateLength(const aetos_msgs::msg::EncoderValues &msg);
  void forwardKinematics();
  void inverseKinematics();
  void uavInBoundSecurityCheck();
  void positionError();
  void updateDesiredPosition();

  void joyVelocityCallback(const aetos_msgs::msg::Velocity &msg)
  {
    auto message = aetos_msgs::msg::MotorVelocity();

    rclcpp::Time currentTime = this->now();
    double dt = 0.01; 

    if (_lastVelocityUpdateTime.nanoseconds() > 0)
    {
      dt = (currentTime - _lastVelocityUpdateTime).seconds();

      if (dt > 0.1)
      {
        dt = 0.1f;
            }
      if (dt <= 0.0)
      {
        dt = 0.01f;
      }
    }

    _lastVelocityUpdateTime = currentTime;

    sVelocity targetVelocity = {msg.velocity_x, msg.velocity_y, msg.velocity_z};

    float max_velocity_change = MAX_ACCEL * dt;

    float vx_diff = targetVelocity.vx - _currentVelocity.vx;
    if (std::abs(vx_diff) > max_velocity_change)
    {
      _currentVelocity.vx += (vx_diff > 0) ? max_velocity_change : -max_velocity_change;
    }
    else
    {
      _currentVelocity.vx = targetVelocity.vx;
    }

    float vy_diff = targetVelocity.vy - _currentVelocity.vy;
    if (std::abs(vy_diff) > max_velocity_change)
    {
      _currentVelocity.vy += (vy_diff > 0) ? max_velocity_change : -max_velocity_change;
    }
    else
    {
      _currentVelocity.vy = targetVelocity.vy;
    }

    float vz_diff = targetVelocity.vz - _currentVelocity.vz;
    if (std::abs(vz_diff) > max_velocity_change)
    {
      _currentVelocity.vz += (vz_diff > 0) ? max_velocity_change : -max_velocity_change;
    }
    else
    {
      _currentVelocity.vz = targetVelocity.vz;
    }

    _velocity.vx = _currentVelocity.vx;
    _velocity.vy = _currentVelocity.vy;
    _velocity.vz = _currentVelocity.vz;

    this->updateDesiredPosition();
    this->forwardKinematics();
    this->uavInBoundSecurityCheck();
    this->inverseKinematics();

    message.omega1 = _motorVelocity.w1;
    message.omega2 = _motorVelocity.w2;
    message.omega3 = _motorVelocity.w3;
    message.omega4 = _motorVelocity.w4;

    _joyVelPub->publish(message);
    _angularVelPub->publish(message);

    this->publish_position(_cameraPosition);
  }

  void encoder_callback(const aetos_msgs::msg::EncoderValues &msg)
  {
    this->updateLength(msg);
  }

  void publish_motor_velocity(const sMotorVelocity &_motorVelocity)
  {
    auto message = aetos_msgs::msg::MotorVelocity();

    message.omega1 = _motorVelocity.w1;
    message.omega2 = _motorVelocity.w2;
    message.omega3 = _motorVelocity.w3;
    message.omega4 = _motorVelocity.w4;

    _joyVelPub->publish(message);
  }

  void publish_position(const sPosition &_cameraPosition)
  {
    auto message = aetos_msgs::msg::EffectorPosition();

    message.position_x = _cameraPosition.x;
    message.position_y = _cameraPosition.y;
    message.position_z = _cameraPosition.z;

    _positionPub->publish(message);
  }

  rclcpp::Subscription<aetos_msgs::msg::Velocity>::SharedPtr _subJoyVelocity;
  rclcpp::Subscription<aetos_msgs::msg::Velocity>::SharedPtr _subAutoVelocity;
  rclcpp::Subscription<aetos_msgs::msg::EncoderValues>::SharedPtr _subEncoder;

  rclcpp::Publisher<aetos_msgs::msg::MotorVelocity>::SharedPtr _joyVelPub;
  rclcpp::Publisher<aetos_msgs::msg::MotorVelocity>::SharedPtr _autoVelPub;
  rclcpp::Publisher<aetos_msgs::msg::MotorVelocity>::SharedPtr _angularVelPub;
  rclcpp::Publisher<aetos_msgs::msg::EffectorPosition>::SharedPtr _positionPub;
};

void VelocityConversion::updateVelocity(const aetos_msgs::msg::Velocity &msg)
{
  _velocity.vx = msg.velocity_x;
  _velocity.vy = msg.velocity_y;
  _velocity.vz = msg.velocity_z;

  this->uavInBoundSecurityCheck();
}

void VelocityConversion::uavInBoundSecurityCheck()
{

  if ((_cameraPosition.x <= Limits::X_MIN && _velocity.vx < 0) || (_cameraPosition.x >= Limits::X_MAX && _velocity.vx > 0))
  {
    RCLCPP_WARN_THROTTLE(this->get_logger(), *this->get_clock(), 2000, "Hit Limits");
    _velocity.vx = 0.0f;
  }
  else if ((_cameraPosition.y <= Limits::Y_MIN && _velocity.vy < 0) || (_cameraPosition.y >= Limits::Y_MAX && _velocity.vy > 0))
  {
    RCLCPP_WARN_THROTTLE(this->get_logger(), *this->get_clock(), 2000, "Hit Limits");
    _velocity.vy = 0.0f;
  }
};

void VelocityConversion::updateLength(const aetos_msgs::msg::EncoderValues &msg)
{
  _cableLength.l1 = msg.angle1 * _radius + _initialCableLength.l1;
  _cableLength.l2 = msg.angle2 * _radius + _initialCableLength.l2;
  _cableLength.l3 = msg.angle3 * _radius + _initialCableLength.l3;
  _cableLength.l4 = msg.angle4 * _radius + _initialCableLength.l4;
}

void VelocityConversion::positionError()
{
  _positionError.x = _desiredPosition.x - _cameraPosition.x;
  _positionError.y = _desiredPosition.y - _cameraPosition.y;
  _positionError.z = _desiredPosition.z - _cameraPosition.z;

  const double threshold = 0.001;

  if (std::abs(_positionError.x) < threshold)
    _positionError.x = 0.0;
  if (std::abs(_positionError.y) < threshold)
    _positionError.y = 0.0;
  if (std::abs(_positionError.z) < threshold)
    _positionError.z = 0.0;

  const float Kp = 0.6f;

  _velocity.vx += Kp * _positionError.x;
  _velocity.vy += Kp * _positionError.y;
  _velocity.vz += Kp * _positionError.z;
}

void VelocityConversion::updateDesiredPosition()
{
  float dt = 0.01f;

  _desiredPosition.x += _velocity.vx * dt;
  _desiredPosition.y += _velocity.vy * dt;
  _desiredPosition.z += _velocity.vz * dt;
}

void VelocityConversion::inverseKinematics()
{
  Eigen::MatrixXf J(4, 3);
  Eigen::VectorXf V(3);
  Eigen::VectorXf Lv(4);

  J(0, 0) = (_cameraPosition.x - _pole1.x) / _cableLength.l1;
  J(0, 1) = (_cameraPosition.y - _pole1.y) / _cableLength.l1;
  J(0, 2) = (_cameraPosition.z - _pole1.z) / _cableLength.l1;

  J(1, 0) = (_cameraPosition.x - _pole2.x) / _cableLength.l2;
  J(1, 1) = (_cameraPosition.y - _pole2.y) / _cableLength.l2;
  J(1, 2) = (_cameraPosition.z - _pole2.z) / _cableLength.l2;

  J(2, 0) = (_cameraPosition.x - _pole3.x) / _cableLength.l3;
  J(2, 1) = (_cameraPosition.y - _pole3.y) / _cableLength.l3;
  J(2, 2) = (_cameraPosition.z - _pole3.z) / _cableLength.l3;

  J(3, 0) = (_cameraPosition.x - _pole4.x) / _cableLength.l4;
  J(3, 1) = (_cameraPosition.y - _pole4.y) / _cableLength.l4;
  J(3, 2) = (_cameraPosition.z - _pole4.z) / _cableLength.l4;

  V(0) = _velocity.vx;
  V(1) = _velocity.vy;
  V(2) = _velocity.vz;

  Lv = J * V;

  float velocityRatio = std::max({abs(Lv(0) / _radius / MAX_WHEEL_VELOCITY),
                                  abs(Lv(1) / _radius / MAX_WHEEL_VELOCITY),
                                  abs(Lv(2) / _radius / MAX_WHEEL_VELOCITY),
                                  abs(Lv(3) / _radius / MAX_WHEEL_VELOCITY)});

  if (velocityRatio > 1.0f)
  {
    Lv /= velocityRatio;
  }

  _motorVelocity.w1 = Lv(0) / _radius;
  _motorVelocity.w2 = Lv(1) / _radius;
  _motorVelocity.w3 = Lv(2) / _radius;
  _motorVelocity.w4 = Lv(3) / _radius;
}

void VelocityConversion::forwardKinematics()
{
  _cameraPosition.x = (_cableLength.l1 * _cableLength.l1 + _arenaLength * _arenaLength - _cableLength.l4 * _cableLength.l4) / (2 * _arenaLength);
  _cameraPosition.y = (_cableLength.l1 * _cableLength.l1 + _arenaWidth * _arenaWidth - _cableLength.l2 * _cableLength.l2) / (2 * _arenaWidth);
  _cameraPosition.z = sqrt(abs(_cableLength.l1 * _cableLength.l1 - _cameraPosition.x * _cameraPosition.x - _cameraPosition.y * _cameraPosition.y));
}

int main(int argc, char *argv[])
{
  rclcpp::init(argc, argv);
  rclcpp::spin(std::make_shared<VelocityConversion>());
  rclcpp::shutdown();
  return 0;
}

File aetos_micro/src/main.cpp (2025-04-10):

#include <Arduino.h>
#include "config.hpp"
#include "QuadratureEncoder.hpp"
#include "TalonSrx.hpp"
#include "Joint.hpp"
#include "PID.hpp"
#include "Serialnterface.hpp"

static constexpr unsigned long READ_VELOCITY_FREQ_HZ = 100ul;
static constexpr unsigned long SEND_ANGLE_FREQ_HZ = 100ul;

void setup()
{
    Serial.begin(115200);

    QuadratureEncoder encoder1 = QuadratureEncoder(PIN_ENCODER_A1, PIN_ENCODER_B1, PCNT_UNIT_0);
    QuadratureEncoder encoder2 = QuadratureEncoder(PIN_ENCODER_A2, PIN_ENCODER_B2, PCNT_UNIT_1);
    QuadratureEncoder encoder3 = QuadratureEncoder(PIN_ENCODER_A3, PIN_ENCODER_B3, PCNT_UNIT_2);
    QuadratureEncoder encoder4 = QuadratureEncoder(PIN_ENCODER_A4, PIN_ENCODER_B4, PCNT_UNIT_3);

    TalonSrx talon1 = TalonSrx(PIN_PWM_1, LEDC_TIMER_0, LEDC_CHANNEL_0);
    TalonSrx talon2 = TalonSrx(PIN_PWM_2, LEDC_TIMER_1, LEDC_CHANNEL_2);
    TalonSrx talon3 = TalonSrx(PIN_PWM_3, LEDC_TIMER_2, LEDC_CHANNEL_3);
    TalonSrx talon4 = TalonSrx(PIN_PWM_4, LEDC_TIMER_3, LEDC_CHANNEL_4);

    PID pid1 = PID(KP, KI, KD, 50.0f);
    PID pid2 = PID(KP, KI, KD, 50.0f);
    PID pid3 = PID(KP, KI, KD, 50.0f);
    PID pid4 = PID(KP, KI, KD, 50.0f);

    Joint joint1 = Joint(&encoder1, &pid1, &talon1);
    Joint joint2 = Joint(&encoder2, &pid2, &talon2);
    Joint joint3 = Joint(&encoder3, &pid3, &talon3);
    Joint joint4 = Joint(&encoder4, &pid4, &talon4);

    SerialCom serialCom = SerialCom(&joint1, &joint2, &joint3, &joint4);
    sRequestedVelocity requestedVelocity;

    Helpers::Timer<unsigned long, micros> _timerReadVelocity =
        Helpers::Timer<unsigned long, micros>(1000000.0f / (float)READ_VELOCITY_FREQ_HZ);

    Helpers::Timer<unsigned long, micros> _timerSendAngle =
        Helpers::Timer<unsigned long, micros>(1000000.0f / (float)SEND_ANGLE_FREQ_HZ);

    encoder1.begin();
    encoder2.begin();
    encoder3.begin();
    encoder4.begin();

    joint1.init();
    joint2.init();
    joint3.init();
    joint4.init();

    for (;;)
    {
        requestedVelocity = serialCom.getVelocityData();

        if (_timerReadVelocity.isDone())
        {
            if (requestedVelocity.homing)
            {
                joint1.resetEncoders();
                joint2.resetEncoders();
                joint3.resetEncoders();
                joint4.resetEncoders();
            }
        }

        joint1.setSpeedRad(requestedVelocity.motor1Velocity);
        joint2.setSpeedRad(requestedVelocity.motor2Velocity);
        joint3.setSpeedRad(requestedVelocity.motor3Velocity);
        joint4.setSpeedRad(requestedVelocity.motor4Velocity);

        if (_timerSendAngle.isDone())
        {
            serialCom.sendEncoderData();
        }

        joint1.update();
        joint2.update();
        joint3.update();
        joint4.update();
    }
}

void loop()
{
}

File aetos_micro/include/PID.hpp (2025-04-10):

#ifndef __PID_HPP__
#define __PID_HPP__

#include <Arduino.h>

class PID
{
public:
    static constexpr unsigned long PERIOD_SPEED_CALC_US = 10'000ul;

    PID(float kp_, float ki_, float kd_, float intergalLimit_);
    ~PID() {}
    void init(void);
    void setGains(float kp_, float ki_, float kd_);
    void setIntLimit(float limit_);
    /// @brief
    /// @param error_ Error between goal and actual position
    /// @return New command
    float computeCommand(float error_);
    /// @brief Resets integral counter and derivative last value to zero
    void reset(void);

private:
    float _kp = 0.0f;
    float _ki = 0.0f;
    float _kd = 0.0f;

    float _cmdI = 0.0f;
    float _lastcmdD = 0.0f;
    float _integralLimit = 0.0f;
    float _previousError = 0.0f;
    float _lastMeasureTime = 0.0f;
};

PID::PID(float kp_, float ki_, float kd_, float intergalLimit_)
{
    this->setGains(kp_, ki_, kd_);
    this->setIntLimit(intergalLimit_);
    this->reset();
    _lastMeasureTime = micros();
}

void PID::init(void)
{
    this->reset();
}

void PID::setGains(float kp_, float ki_, float kd_)
{
    _kp = kp_;
    _ki = ki_;
    _kd = kd_;
}

void PID::setIntLimit(float limit_)
{
    _integralLimit = abs(limit_);
}

float PID::computeCommand(float error_)
{
    if (isnan(error_))
    {
        error_ = 0.0f;
    }
    if (isinf(error_))
    {
        error_ = 0.0f;
    }

    _cmdI += _ki * error_;

    float cmdP = _kp * error_;
    _cmdI = constrain(_cmdI, -_integralLimit, _integralLimit);

    float cmdD = 0.0f;
    float currentTime = micros();
    if (currentTime - _lastMeasureTime > PERIOD_SPEED_CALC_US)
    {
        float dt = currentTime - _lastMeasureTime;
        _lastMeasureTime = currentTime;

        cmdD = _kd * (error_ - _previousError) / (dt / 1'000'000.0f);
        _lastcmdD = cmdD;
    }
    else
    {
        cmdD = _lastcmdD;
    }

    if (isnan(cmdP))
    {
        cmdP = 0.0f;
    }
    if (isnan(_cmdI))
    {
        _cmdI = 0.0f;
    }
    if (isnan(cmdD))
    {
        cmdD = 0.0f;
    }

    _previousError = error_;

    return cmdP + _cmdI + cmdD;
}

void PID::reset(void)
{
    _cmdI = 0.0f;
    _previousError = 0.0f;
}

#endif // __PID_HPP__

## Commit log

2025-01-25 added mounts and args for device connection
2025-01-25 print left & right joystick values
2025-01-26 Creation of a publisher and subscriber in C++ for the velocity
2025-01-27 Changes upon PR review
    Still issues to fix before merge
    [main.cpp, serial_com.cpp]
2025-01-29 changed buttons config and tested with msgs w/ subscriber
2025-01-31 correction of the subscriber
    [velocity_conversion.cpp]
2025-02-01 Little correction from PR comments
    [main.cpp]
2025-02-04 timer + working motor driver class
2025-02-05 added PID class from rover
2025-02-05 removed prints
2025-02-05 Encoder basic class
2025-02-05 New base for serial and joint class
2025-02-05 Direct Kinematics
2025-02-10 working motor and encoder class
2025-02-11 Auto stash before rebase of "dev/simulation_NP" onto "origin/dev/velocity_calculation_ELB"
2025-02-11 First solid iteration of joint class
2025-02-11 simulation working, subscribing to effector_position & motor_velocity and publishing on encoder_values topic
2025-02-11 Serial interface + joint update
2025-02-16 Joint receive fct to test and new base for ros2 serial interface
2025-02-17 Updated joint
2025-02-19 joy_demux communicates w/ velocity_conversion + merges corrections
    [velocity_conversion.cpp]
2025-03-09 Issue with serial comm
    [main.cpp, serial_com.cpp]
2025-03-11 Communication with raspberry pi and publication of the vision node data
2025-03-12 Adaptation for kinematic node
2025-03-19 Revert "Working arbitration"
    This reverts commit 4b1387791ed0a34115f028931b7cd39197b2d650.
    [arbitration.cpp, serial_com.cpp, velocity_conversion.cpp]
2025-03-19 Reset to arbitration commit
    [arbitration.cpp]
2025-03-19 Ajout de thread
2025-03-25 ui communicates with arbitration w/o crashing, not tested yet
    [arbitration.cpp]
2025-03-26 Add sharing video data and velocity on aetos/cam/velocity and aetos/cam/video
2025-04-02 Base for position pid
2025-04-02 Working pid position
2025-04-02 Added links to BOM
2025-04-09 Added mathybou-patch to doc
    [Box - Box.stl, Box- Door.stl, Pulley - Bas centre hinge.stl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]
2025-04-09 Added esp32-platformio doc
2025-04-09 Deadman + reset encoders implemented
2025-04-10 Finished Mec doc
    [Box - Box.stl, Box- Door.stl, Frame - Homing1.stl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]
